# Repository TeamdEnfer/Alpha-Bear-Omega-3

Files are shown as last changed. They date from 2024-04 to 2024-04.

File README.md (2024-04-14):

# Alpha-Bear-Omega-3 ($\alpha-$:bear: $-\Omega-\pi$)

  

$\alpha-$:bear: $-\Omega-\pi$ | The **better-ish**(?) quadruped robot | UdeS-GRO-68

Inspired by project [QuadrUS](https://github.com/olivierfournier2/S4H2021-QuadrUS), Boston Dynamics' [Spot](https://bostondynamics.com/products/spot/) and MIT's [mini cheetah](https://news.mit.edu/2019/mit-mini-cheetah-first-four-legged-robot-to-backflip-0304),  $\alpha-$:bear: $-\Omega-\pi$ is a quadruped robot bear made by six robotics engineering students from [Université de Sherbrooke](https://www.usherbrooke.ca/).

## Original Contributors

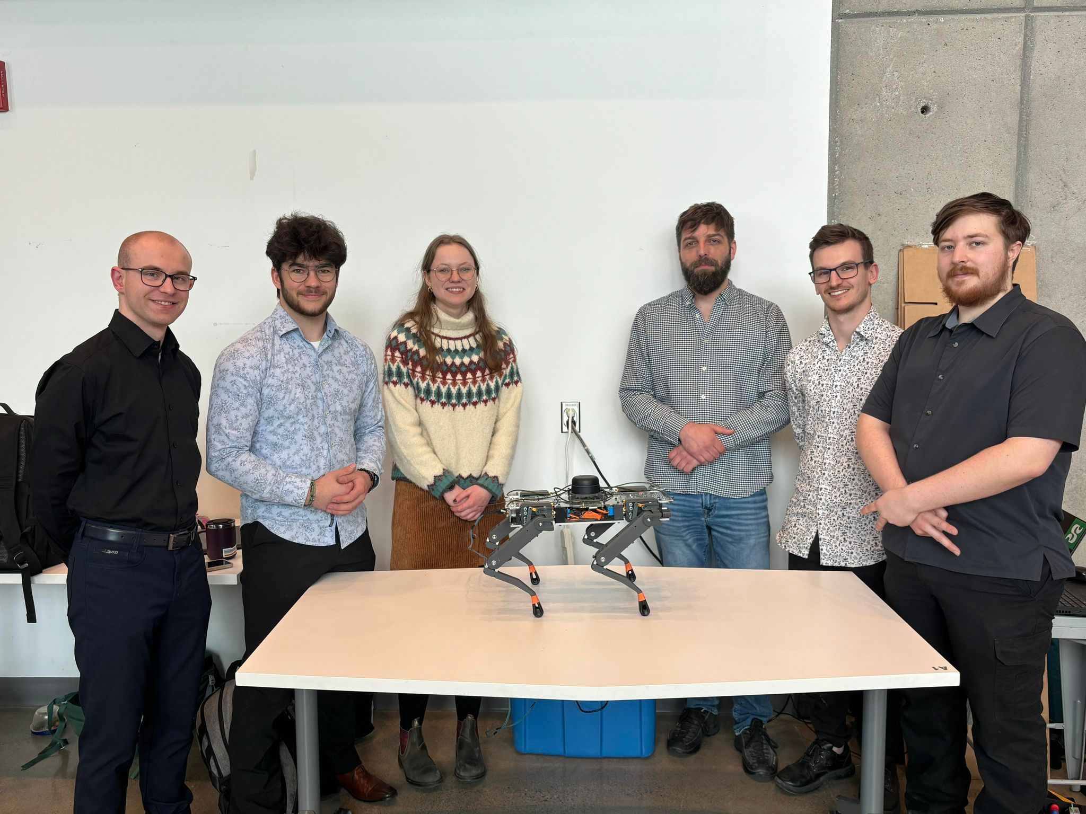
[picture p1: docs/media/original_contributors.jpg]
original_contributors


**From left to right:**

[Marc-Olivier Fecteau](https://github.com/MarcOlivierFecteau)  
[Hubert Houle](https://github.com/Hubert-Houle)  
[Justine Landry](https://github.com/justinelandry2)  
[Jonathan Perron](https://github.com/JPerron774)  
[Alex Jacques](https://github.com/AlexJacquesUS)  
[Thomas-Xavier Guimont](https://github.com/Revixa1)  

### A word from the authors

> We could say that when we chose to make a quadruped robot from scratch in 12 weeks, we wanted to prove to ourselves that we could achieve anything by working together, but we really just wanted to make something cool, and when brainstorming, the idea of a robot bear came up. Why a bear? Because bears can't be intimidated by dogs; thenceforth, robot bears are inherently better.

## Final product

gif_robot

## Table of contents

- [Development environment](#development-environment)
  - [Pre-requisites](#pre-requisites)
  - [Dependencies installation](#dependencies-installation)
  - [Using the installation script](#using-the-installation-script)
- [Robot environment](#robot-environment)
  - [System requirements](#system-requirements)
  - [Packages](#rpi-packages)
  - [Setup SSH](#setup-ssh)

## Development environment

### Pre-requisites

#### Operating system

- [Ubuntu 20.04 LTS](https://releases.ubuntu.com/focal/)

#### Packages

***N.B.*** The [installation script](#using-the-installation-script) installs most of the required packages. It is recommended to first run the script, and then [install the missing dependencies](#dependencies-installation).

- [ROS Noetic](http://wiki.ros.org/noetic/Installation/Ubuntu)
- Rviz: choose `Desktop-Full Install` option when installing ROS
- [CHAMP | champ](https://github.com/chvmp/champ)
- [CHAMP | champ setup assistant](https://github.com/chvmp/champ_setup_assistant)
- [Webots](https://cyberbotics.com/)
- [ROS Joy](http://wiki.ros.org/joystick_drivers)

### Dependencies installation

- Go to [ros-noetic installation page](https://wiki.ros.org/noetic/Installation/Ubuntu) and install ros-noetic.

- Install all dependencies for kinematics:

```bash
sudo apt install python3-pip ros-noetic-joy ros-noetic-rosserial ros-noetic-rosserial-python ros-noetic-rosserial-arduino
```

- Install all depencies for control:

```bash
sudo apt install ros-noetic-ros-control ros-noetic-robot-state-publisher ros-noetic-control-msgs
```

### Using the installation script

&emsp;***N.B.*** Cloning the repository and using the installation script, a **catkin workspace** is initialized, so there's no need to do this procedure.

Choose the directory you want the project cloned into (`~` by default):

```bash
cd ~/<path_to_directory>
```

Then, type:

```bash
git clone --recursive https://github.com/TeamdEnfer/Alpha-Bear-Omega-3.git
```

Then, go into the project repository, launch the install script, and choose what you want to install (`all` option is recommended for first install):

```bash
cd Alpha-Bear-Omega-3
source install.sh
```

Finally, go into the **catkin workspace** and build the ROS workspace:

```bash
cd control/ros_ws
catkin_make
```

The ROS environment should now be set up and ready to work with.

Project setup notes:

> - Every time a non-`.launch` file is modified, do `catkin_make` in the **ros_ws** directory to update the executables.
> - Every time a new terminal is opened, run the `source ./install.sh` script with option `6` to source the ROS setup files. Alternatively, add the command to the `.bashrc` file to automate the process.

## Robot environment

### System requirements

- RaspberryPi 4 (Tested with 8GB RAM)
- [Ubuntu 20.04 LTS](https://releases.ubuntu.com/focal/) (Tested with Server install)

&emsp;***Authors note:*** though we recommend installing Ubuntu Server on the RPi 4, our experience with tha installation was "painful and full of adventures". Good luck!

### RPi Packages

- [ROS Noetic](http://wiki.ros.org/noetic/Installation/Ubuntu)

### Setup SSH

- [Setup RPi as Wi-Fi access point](https://gist.github.com/ExtremeGTX/ea1d1c12dde8261b263ab2fead983dc8)

To access the RPi, type:

```bash
ssh <RPi_name>@<RPi_access_point>
```

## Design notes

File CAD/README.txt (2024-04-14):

Voici une description de la nomenclature pour les fichier de CAD pour le projet de session S4 en génie robotique
Les nom des fichiers sont en minuscule avec des _ pour séparer les mots.

x_y_concept_composante_extra_extra_z
_______________________________________________________________________________________
x:   		Choix de Conception Générale
		 	-0:Système avec poulie dentelée et courroie
_______________________________________________________________________________________
y:   		Version du concept Général
			-1: Système de poulie pour le Tibia et pour le Fémur
		 	-2: Système de poulie pour le Tibia et Barre pour le Fémur
_______________________________________________________________________________________
concept:	pour l'instant, représente le choix de conception comme x mais 
		sera décrit en mot. **sujet à changement vue la répétition
		 	-belt
			-directDrive 	
_______________________________________________________________________________________
composante:   	Nom de la pièce en question
			-body
		 	-femur
		 	-shaft
		 	-bar_trouee
_______________________________________________________________________________________
extra_extra:	Utilisée pour donner des informations suplémentaires sur la pièce.
		 	-60mm_en_L
		 	-simple_right
			-court
_______________________________________________________________________________________
z:   		Version de la pièce particulière auquel le nom est attaché.
_______________________________________________________________________________________

QUELQUES EXEMPLES:
	0_2_1_belt_epaule_1:	première version de l'épaule pour le système de drive belt pour
				le tibia et la barre pour le fémur
	0_0_2_belt_femur_une_piece1_0

*À noter qu'il est possible qu'une même pièce soit utilisé dans deux concept différent.
 Dans ce cas, le numéro de la version origionale est concervé.

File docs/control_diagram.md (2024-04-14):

# ROS | Nodes and topics diagram

::: mermaid

%%{ init: { 'flowchart': { 'curve': 'catmullRom' } } }%%

flowchart TB;
    subgraph RPi4B
        direction TB
        PiNode([RPi 4B])
        rplidar[[RPLIDAR]]

        rplidar -- distances --> PiNode
    end

    subgraph CHAMP
        direction LR
        velocity_smoother([velocity smoother])
        trajectory_controller([trajectory controller])
        teleop([teleop])

        imu/data[IMU data]
    end

    subgraph Arduino Mega
        direction BT
        ArduiNode([Arduino Mega])
        servos[["Servos (x12)"]]

        ArduiNode -- "servo cmd" --> servos
    end

    subgraph Arduino Uno
        direction TB
        BNode([Arduino Uno])
        bno[[BNO]]
        bno-- quaternion --> BNode
    end

    bno_feedback_topic[BNO feedback]

    BNode --> bno_feedback_topic
    bno_feedback_topic --> imu/data
    
    subgraph GUI
        GUI_Node([GUI])
    end

    servo_id_topic[servo id]
    servo_cmd_topic[servo cmd]

    GUI_Node --> servo_id_topic
    GUI_Node --> servo_cmd_topic

    subgraph Controller
        direction TB
        joystick[[Controller]]
        joyNode([Joy])

        joystick -- inputs --> joyNode
        joyNode -- magic --> teleop

    end
:::

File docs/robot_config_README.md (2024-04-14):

Fichiers à modifier pour champ

# Chemin des fichiers de configuration du robot

**URDF:** control/ros_ws/src/alphabearomega3/worlds/Robot  
**Joints:** control/ros_ws/src/alphabear_config/config/joints/joints.yaml  
**Links:** control/ros_ws/src/alphabear_config/config/links/links.yaml  
**Gait:** control/ros_ws/src/alphabear_config/config/gait/gait.yaml  
**Référence des paramètres du gait:** control/ros_ws/src/champ_setup_assistant/docs/images/gait_parameters.png  

# Paramètres du gait

### Paramètres à ne pas modifier

* knee_orientation
* pantograph_leg

### Paramètres pouvant être modifiés

* **odom_scaler :** facteur d'échelle pour compensation d'erreurs d'odométrie [1.0, 1.2]
* **max_linear_velocity_x :** vitesse max avant/arrière (m/s)
* **max_linear_velocity_y :** vitesse max déplacement vers gauche/droite (m/s)
* **max_angular_velocity_z :** vitesse max rotation (rad/s)
* **com_x_translation :** offset du point de référence dans l'axe X (i.e. compenser si centre de masse de la jambe pas aligné avec l'épaule) (m)
* **swing_height :** distance entre le sol et le centre de la patte au point le plus haut de l'élévation (m)
* **stance_depth :** delta distance du genou au point le plus bas durant un cycle (m)
* **stance_duration :** temps qu'une jambe passe appuyée au sol durant un cycle (s)
* **nominal_height :** distance entre l'épaule et le sol durant un cycle (m)

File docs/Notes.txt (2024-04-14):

En regardant Quadrus, l'interaction cmd<-->feedback ressemble a ceci:

Sur le arduino:

    Setup:
        initialisation (voir rosInit dans qd_hw_control.cpp)
            -Dans l'init, on le subscriber cmd_sub surveille le topic hw_cmd (voir definition de cmd_topic)
            -Dans l'init, on advertise le publisher feedback_pub, qui publish sur le topic hw_feedback (voir definition de feedback_topic)

    Subscriber:
        -Le subscriber prend des message multiarray
        -Surveille le topic cmd_topic
        -Utilise la fonction subscriberCallback
            -Cette fonction recois les angle (via hw_cmd) et envoie la commande aux moteurs
    
    Publisher:
        -Le publisher (feedback_pub) envoie des message multiarray et est lier au topic hw_feedback

    Loop:
        -Utilise la fonction readAngles, laquelle va chercher les angles et les store dans le message multiarray feedback_msg
        -Publish feedback_msg avec le publisher feedback_pub.
        -spinonce()
        -delay selon la frequence voulue

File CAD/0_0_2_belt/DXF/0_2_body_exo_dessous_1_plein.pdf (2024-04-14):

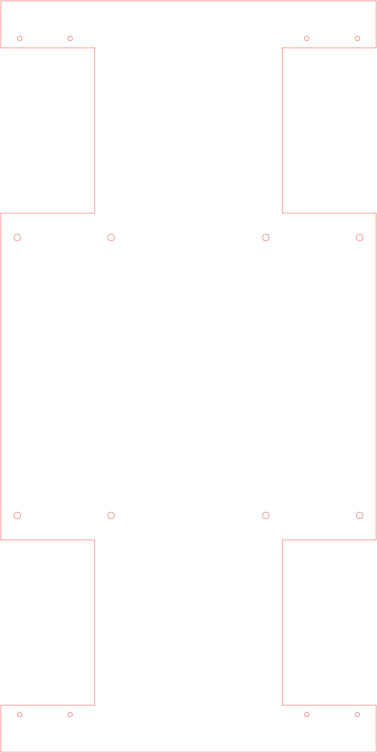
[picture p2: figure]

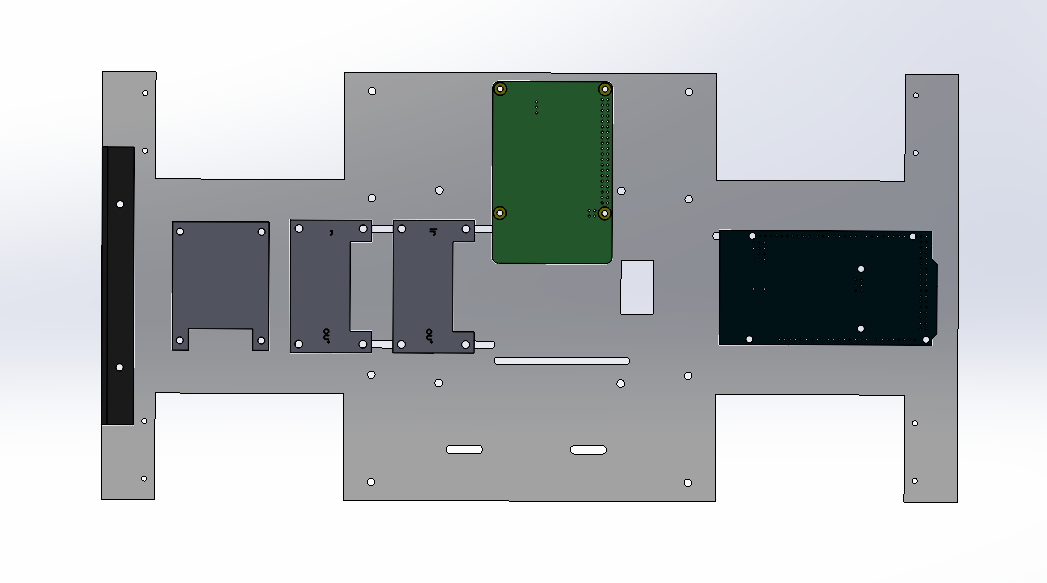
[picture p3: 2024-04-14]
docs/CAD_pictures/Electronics_layout.png

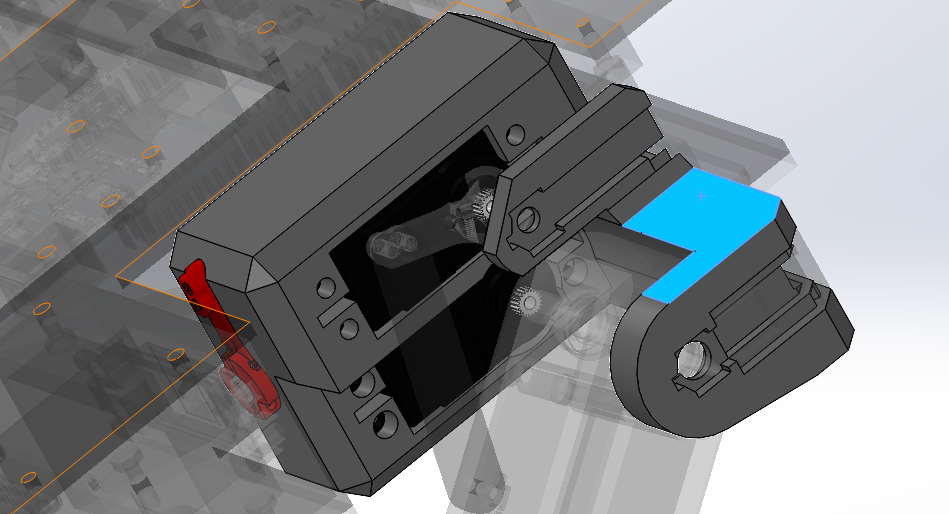
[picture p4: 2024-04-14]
docs/CAD_pictures/Shoulder_servo_ass.png

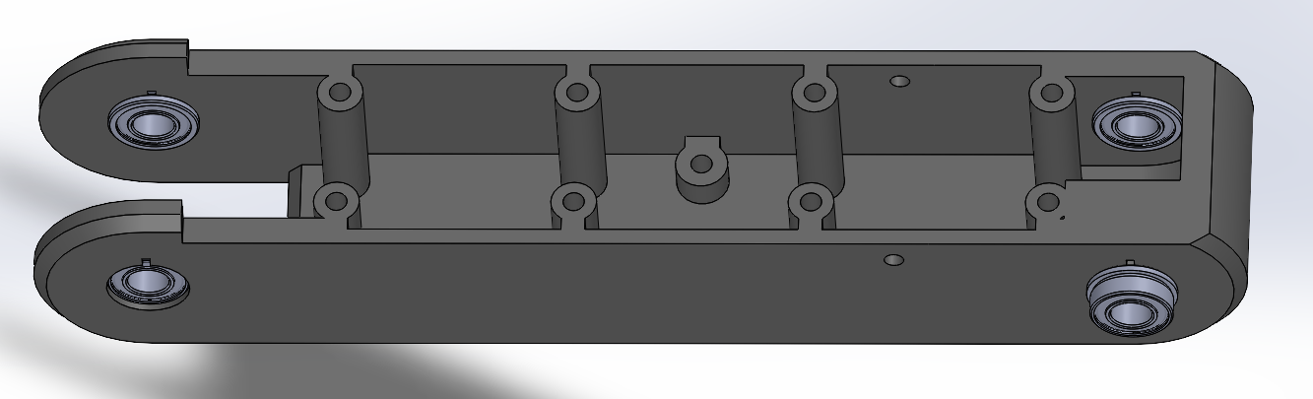
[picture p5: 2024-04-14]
docs/CAD_pictures/femur_bearings.png

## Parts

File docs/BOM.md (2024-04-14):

# BOM

## Hardware

- [ ] GT2 timing belt pulley 20 teeth 6.35mm bore (x4) [(Amazon)](https://a.co/d/ibclgCi)
- [ ] GT2 timing belt pulley 36 teeth 5mm bore (x4) [(Amazon)](https://a.co/d/5uwTJrM)
- [ ] 6.35mm flange coupling  connectors (x4) [(Amazon)](https://a.co/d/h0BUPP9)

## Electronics

- [ ] Arduino Mega 2560 Rev3 [(Arduino)](https://store-usa.arduino.cc/products/arduino-mega-2560-rev3?selectedStore=us)
- [ ] Arduino Uno Rev3 [(Arduino)](https://store-usa.arduino.cc/products/arduino-uno-rev3?selectedStore=us)
- [ ] Raspberry Pi 4 Model B [(Canakit)](https://www.canakit.com/raspberry-pi-4-8gb.html) | [(PiShop.ca)](https://www.pishop.ca/product/raspberry-pi-4-model-b-8gb/) (8GB RAM used)
- [ ] Adafruit BNO055 [(Adafruit)](https://www.adafruit.com/product/2472)
- [ ] Slamtec RPLIDAR A3 [(RobotShop)](https://ca.robotshop.com/fr/products/slamtec-rplidar-a3-360-laser-scanner-25-m)
- [ ] 35 kg.cm servomotors (x12) [(Amazon)](https://www.amazon.ca/s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)
- [ ] 12V-5V DC-DC USB-C converter [(Amazon)](https://a.co/d/4bkU4Bg)
- [ ] 20A 300W 6-40V to 1.2-36V adjustable DC-DC converter (x2) [(Amazon)](https://a.co/d/coVxflM)
- [ ] Power supply: 180W laptop charger (we used one that had a broken cable, so we soldered our own cable)
- [ ] 22|20 AWG wire (for data cables)
- [ ] (At least) 18 AWG wire (for power cables)
- [ ] Dupont connectors
- [ ] U-Type fork terminal electrical wire crimp connectors [(Amazon)](https://www.amazon.ca/s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)
- [ ] WAGO wire connectors [(Amazon)](https://www.amazon.ca/s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)

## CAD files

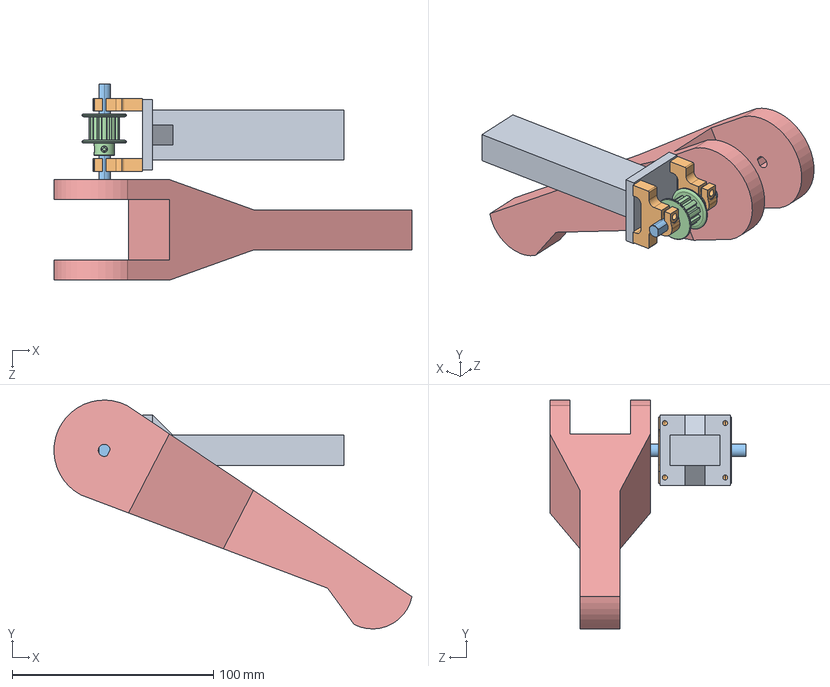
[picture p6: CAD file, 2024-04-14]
CAD/0_0_2_belt_BACK-UP_19_JANVIER/Assem1_tibia_2.SLDASM
177.9 x 113.7 x 97.6 mm
0_0_2_belt_tibia_1
634068.step
1277N711_Corrosion-Resistant Timing Belt Pulley
0_0_1_belt_tibia_1

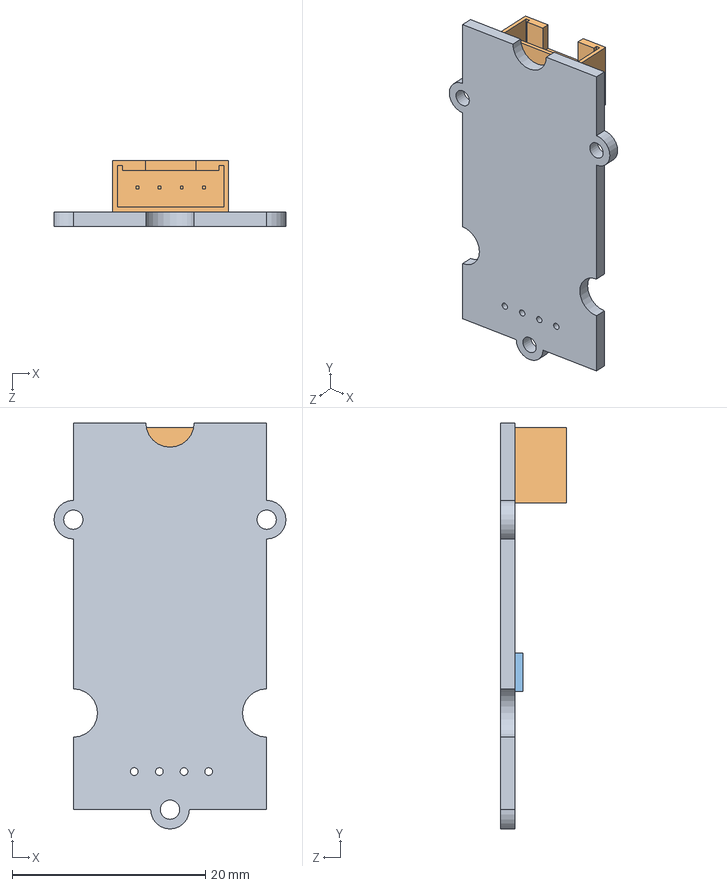
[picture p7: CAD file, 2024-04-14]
CAD/CAD_Web/Grove IMU.SLDASM
24.0 x 42.0 x 6.80 mm
Grove IMU Board
Grove Connecteur
MPU9150

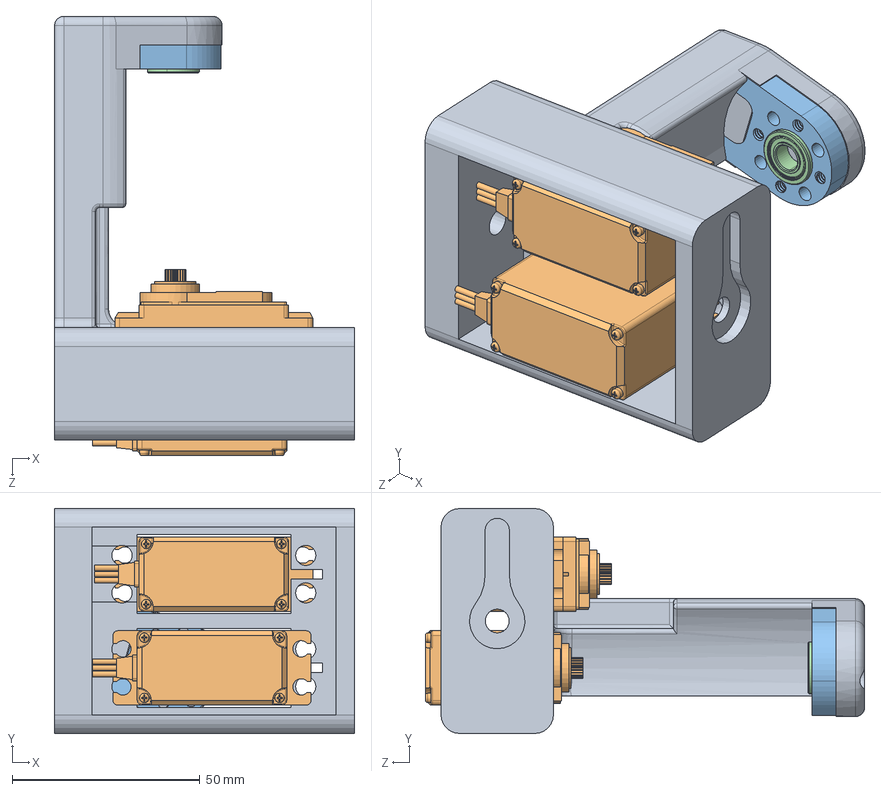
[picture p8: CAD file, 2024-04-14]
CAD/0_0_2_belt/0_2_epaule_1.SLDASM
80.0 x 60.0 x 117.2 mm
0_2_epaule_sprint2_deux_config_JO
hs-422_sws x 2
545404_shaft_adapter_90
535198_bearing

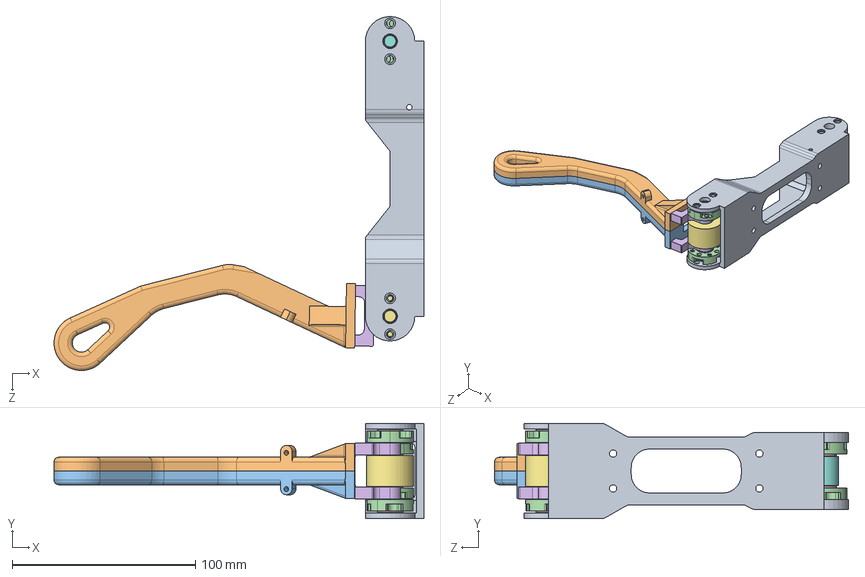
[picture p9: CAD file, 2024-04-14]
CAD/0_0_3_Final/Alexx/0_2_jambe_1.SLDASM
201.8 x 52.0 x 193.1 mm
0_2_femur_une_piece_1
0_2_tibia_2_D
0_2_tibia_2_G
545440.step x 4
535198_bearing x 4
0_2_poulie_grosse_home
0_2_poulie_petite_home

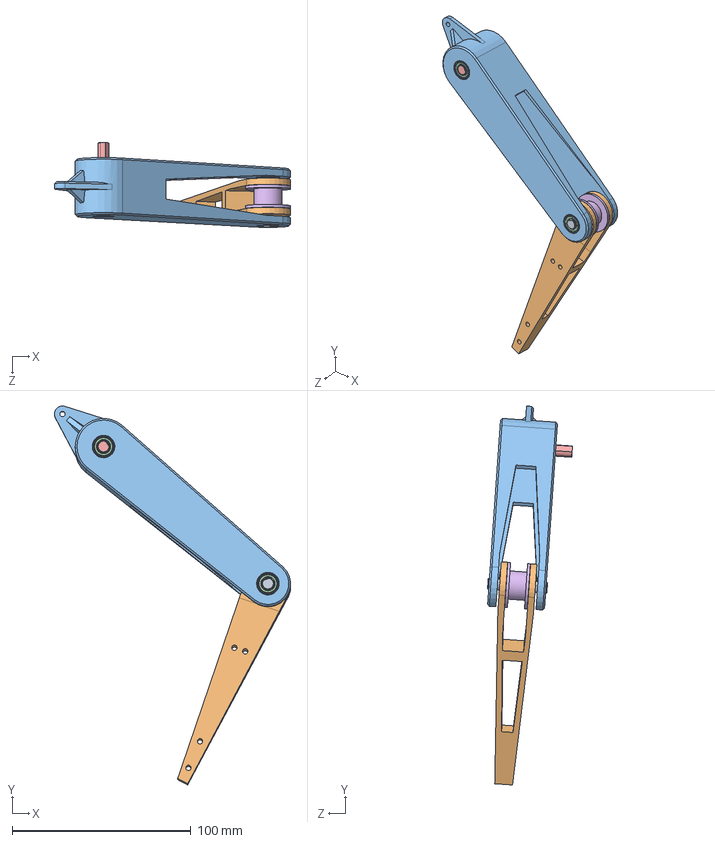
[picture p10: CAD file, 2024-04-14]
CAD/Marco/Marco_concept_SP01_v2/jambe_assemblage.SLDASM
132.3 x 212.3 x 47.6 mm
634088_12in_shaft_cut_tibia
tibia_v2
femur_v2
535198_bearing x 4
634088_12in_shaft_cut_femur
poulie_at_home

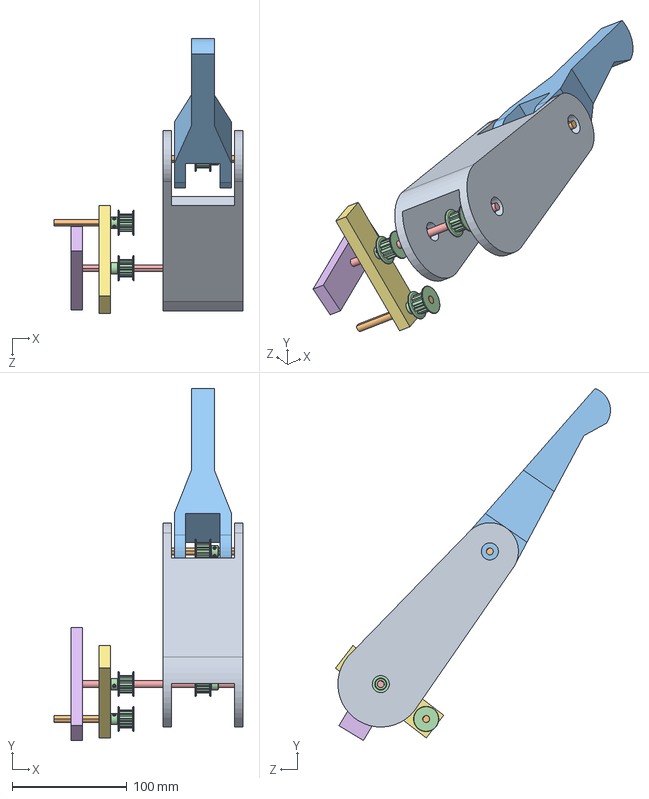
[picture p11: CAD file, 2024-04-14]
CAD/0_0_1_belt/Assem1.SLDASM
165.0 x 307.4 x 240.2 mm
0_0_1_belt_femur_1
0_0_1_belt_6mmShaft_1 x 2
0_0_1_belt_tibia_1
1277N711_Corrosion-Resistant Timing Belt Pulley x 4
0_0_1_belt_6mmX15mmShaft_1
0_0_1_belt_6mm_manivelle_1
0_0_1_belt_guideShaft75mm_1

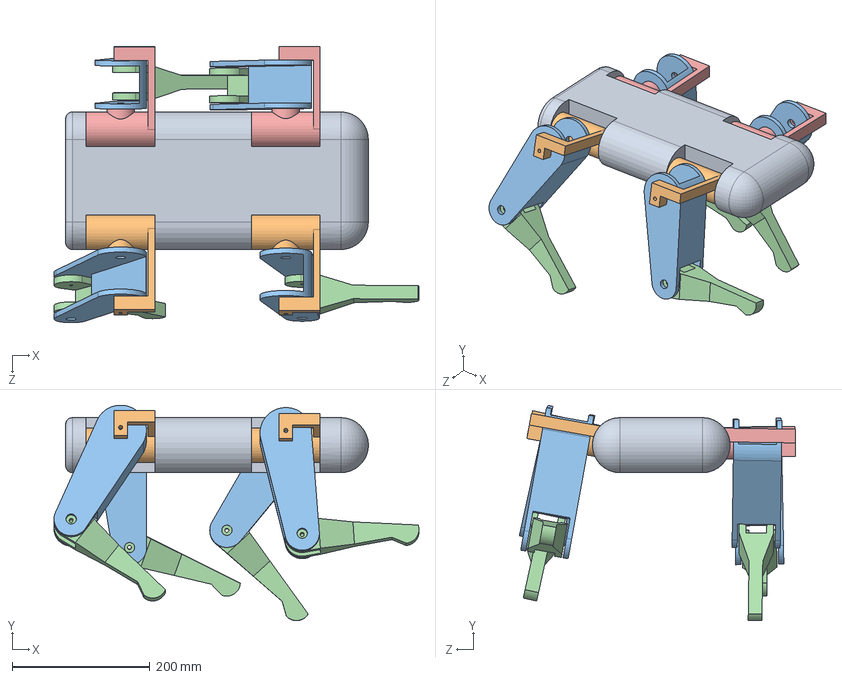
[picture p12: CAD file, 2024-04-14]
CAD/0_0_2_belt_BACK-UP_19_JANVIER/0_1_assemblage_robot_complet_1.SLDASM
530.3 x 313.1 x 401.6 mm
0_0_1_belt_body
0_0_1_belt_epaule_1 x 2
0_0_1_belt_femur_1 x 4
0_0_1_belt_tibia_1 x 4
0_0_1_belt_epaule_l_1 x 2

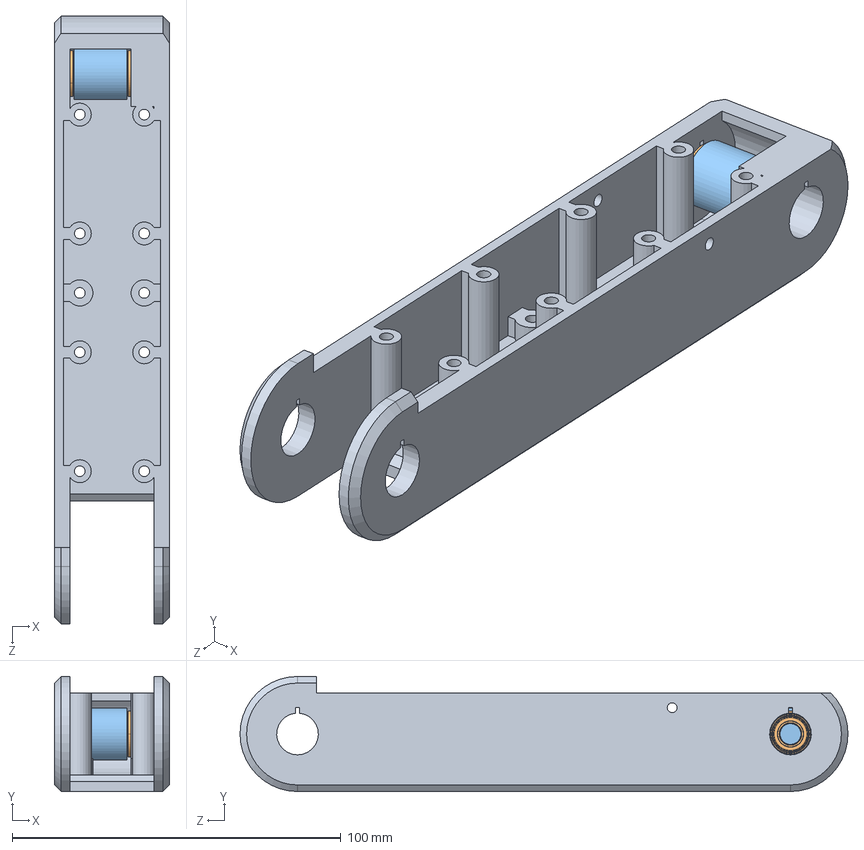
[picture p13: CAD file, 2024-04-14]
CAD/0_0_3_belt/Assem1.SLDASM
35.0 x 35.0 x 185.0 mm
0_0_3_femur_ferme_dessous_1
535198_bearing x 2
0_2_poulie_petite_home

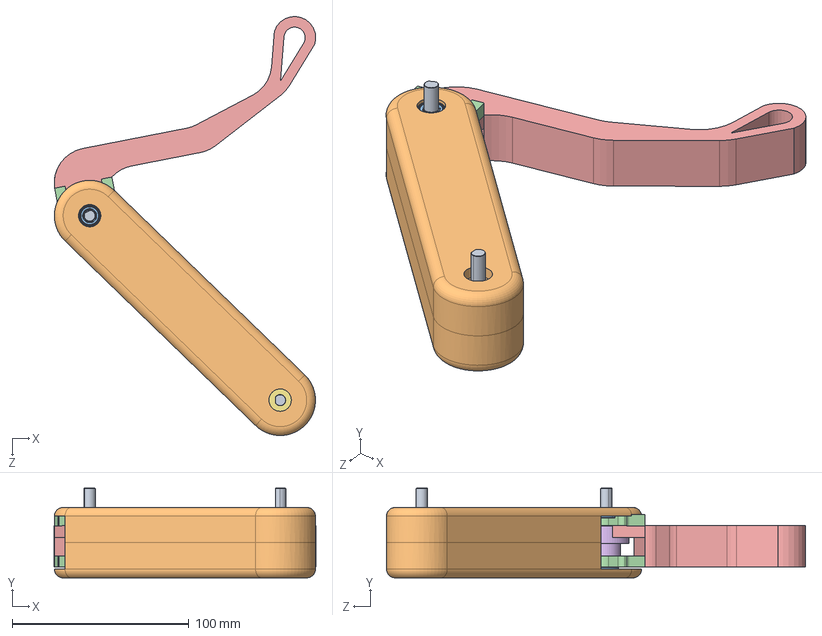
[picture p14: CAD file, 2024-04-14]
CAD/0_0_3_belt/0_0_3_belt_Assem1.SLDASM
147.9 x 50.8 x 237.0 mm
634068.step x 2
0_0_3_femur_simple_1 x 2
535198_bearing x 2
0_0_3_tibia_simple_1
0_2_poulie_grosse_home
0_2_poulie_petite_home

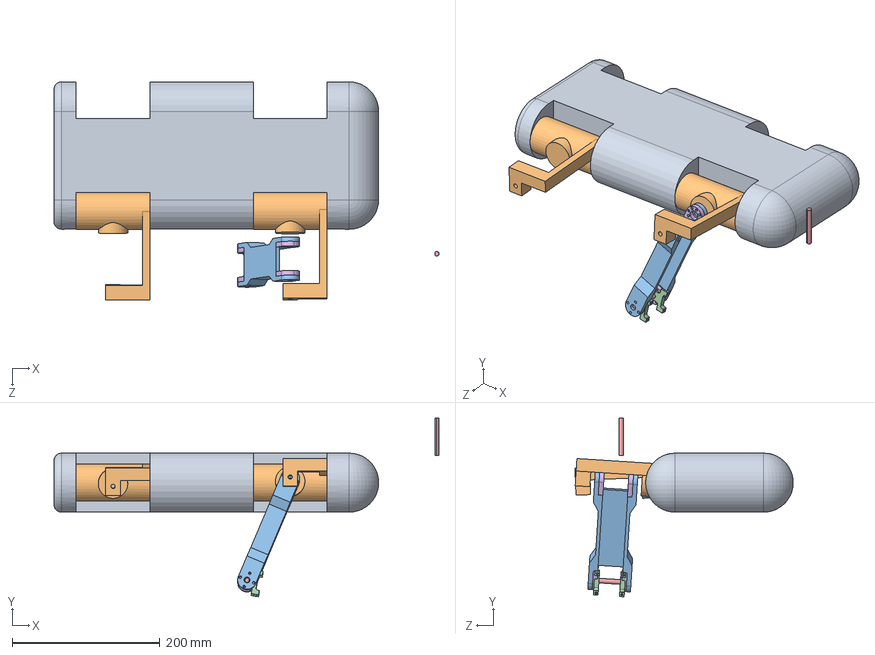
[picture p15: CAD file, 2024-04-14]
CAD/0_0_2_belt_BACK-UP_19_JANVIER/0_2_assemblage_robot_complet_1.SLDASM
521.7 x 242.2 x 295.9 mm
0_0_1_belt_body
0_0_1_belt_epaule_1 x 2
0_0_2_belt_femur_une_piece1_0
634068.step x 2
545404_shaft_adapter_90 x 4

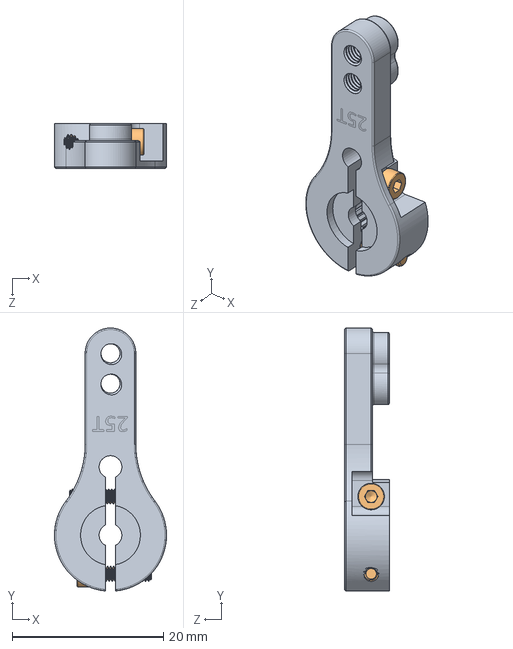
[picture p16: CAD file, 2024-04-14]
CAD/CAD_Web/SERVO ARM HORN 25T ALUMINIUM/SERVO ARM HORN WITH FASTENERS.SLDASM
14.8 x 34.7 x 5.90 mm
SERVO ARM HORN 25T ALUMINIUM
M2 CAP HEAD SOCKET SCREW x 2

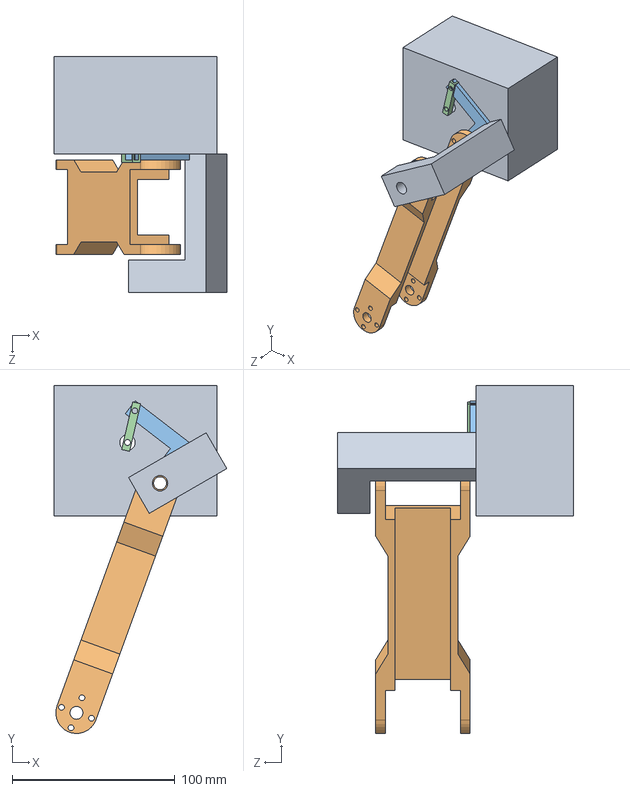
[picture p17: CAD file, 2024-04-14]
CAD/0_0_2_belt_BACK-UP_19_JANVIER/0_2_assemblage_sprint1_1.SLDASM
106.0 x 213.6 x 145.0 mm
0_0_2_belt_epaule_R_1
0_0_2_belt_femur_une_piece1_0
0_0_2_belt_90mm_bar_trouee_enL
0_0_2_belt_20mm_bar_I

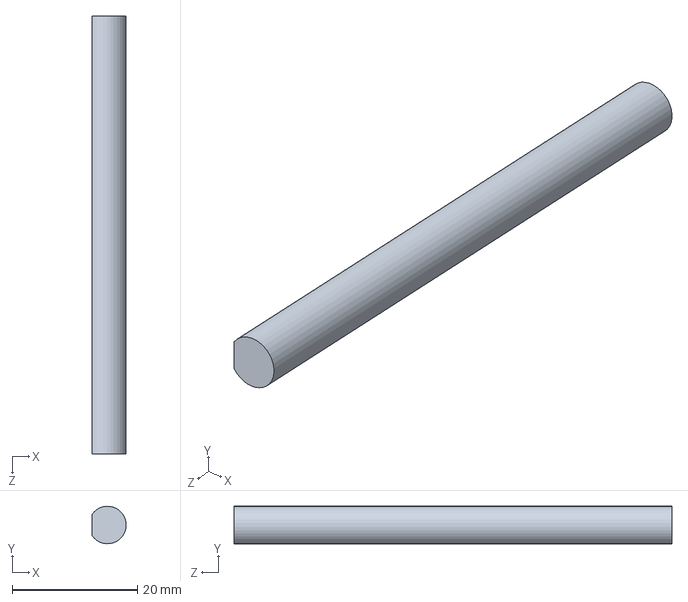
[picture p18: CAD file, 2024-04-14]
CAD/0_0_1_belt/0_0_1_belt_6mmShaft_1.SLDPRT
5.49 x 6.00 x 70.0 mm

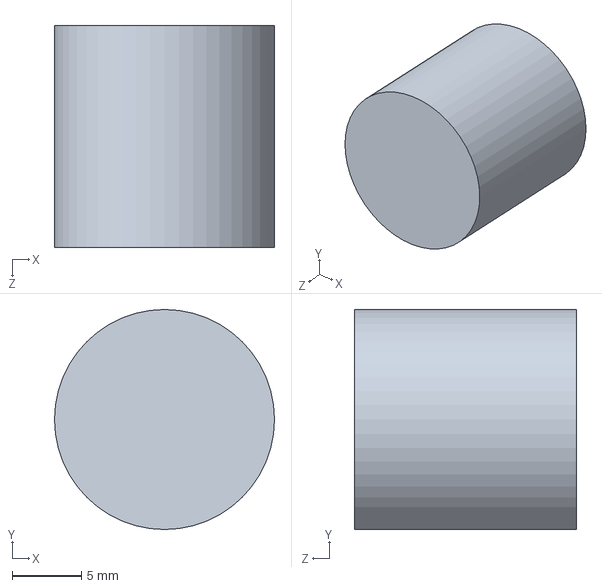
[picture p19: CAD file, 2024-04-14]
CAD/0_0_2_belt/0_2_poulie_petite_home.SLDPRT
15.9 x 15.9 x 16.0 mm

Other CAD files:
CAD/0_0_2_belt/0_2_jambe_1.SLDASM
CAD/0_0_2_belt/3MF/print_0_2_bar_trouee_en_C_35mm_1.3MF
CAD/0_0_2_belt/DXF/0_2_body_exo_dessous_1__EXO.DXF
CAD/0_0_1_belt/0_0_1_belt_6mmX15mmShaft_1.SLDPRT
CAD/0_0_1_belt/0_0_1_belt_6mm_manivelle_1.SLDPRT
CAD/0_0_1_belt/0_0_1_belt_femur_1.SLDPRT
CAD/0_0_1_belt/0_0_1_belt_guideShaft75mm_1.SLDPRT
CAD/0_0_1_belt/0_0_1_belt_tibia_1.SLDPRT
CAD/0_0_2_belt/0_2_bar_trouee_50mm_1.SLDPRT
CAD/0_0_2_belt/0_2_body_exo_dessous_1.SLDPRT
CAD/0_0_2_belt/0_2_body_exo_dessous_1_MEP.SLDDRW
CAD/0_0_2_belt/0_2_epaule_sprint2_deux_config.SLDPRT
CAD/0_0_2_belt/0_2_epaule_sprint2_deux_config_JO.SLDPRT
CAD/0_0_2_belt/0_2_femur_une_piece_1.SLDPRT
CAD/0_0_2_belt/0_2_poulie_grosse_home.SLDPRT
CAD/0_0_2_belt/0_2_spacer_avec_trou_1.SLDPRT
CAD/0_0_2_belt/0_2_support_abduction_servo_1.SLDPRT
CAD/0_0_2_belt/0_2_tibia_2_D.SLDPRT
CAD/0_0_2_belt/0_2_tibia_2_G.SLDPRT
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

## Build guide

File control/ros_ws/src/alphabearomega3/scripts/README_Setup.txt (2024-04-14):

Etapes pour starter ROS sur le Pi, ainsi que la communication Rosserial

1: SSH sur le pi
2: roscore &
3: rosrun rosserial_python serial_node.py /dev/ttyACM0 & 

Nom du topic: /servo
    Format du message: rostopic pub /servo  std_msgs/UInt16 "data: 0"
    ou data: est un angle donner a un servo lier a la pin D13

Nom du node: /serial_node

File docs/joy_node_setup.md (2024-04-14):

# Button mapping for controllers

Button maps for other controllers can be found [here](http://wiki.ros.org/joy#Application)

## Xbox One controller

### Axes

0: Joystick gauche: gauche <-> droite \[-32767, 32767\]  
1: gauche: haut <-> bas \[-32767, 32767\]  
2: Trigger (analog) gauche \[-32767, 32767\]  
3: Joystick droite: gauche <-> droite \[-32767, 32767\]  
4: Joystick droit: haut <-> bas \[-32767, 32767\]  
5: Trigger (analog) droite \[-32767, 32767\]  
6: D-pad gauche <-> droite {-32767, 32767}  
7: D-pad haut <-> bas {-32767, 32767}

	N.B. ROS: [-1.0, 1.0], {-1.0, 1.0}

### Boutons

0: A  
1: B  
2: X  
3: Y  
4: Bumper gauche  
5: Bumper droit  
6: Select  
7: Start  
8: Power/Menu  
9: Joystick gauche: appui  
10: Joystick droit: appui

## PlayStation 3 controller

### Axes
0: Joystick gauche: gauche <-> droite \[-32767, 32767\]  
1: gauche: haut <-> bas \[-32767, 32767\]  
2: Trigger (analog) gauche \[-32767, 32767\]  
3: Joystick droite: gauche <-> droite \[-32767, 32767\]  
4: Joystick droit: haut <-> bas \[-32767, 32767\]  
5: Trigger (analog) droite \[-32767, 32767\]

### Boutons

0: X  
1: O  
2: 🔺  
3: 🟥  
4: Bumper gauche  
5: Bumper droit  
6: Trigger gauche (bool)  
7: Trigger droit (bool)  
8: Select  
9: Start  
10: Power/Menu  
11: Trigger gauche: appui  
12: Trigger droit: appui  
13: D-pad Up  
14: D-pad Down  
15: D-pad Left  
16: D-pad Right

# Making the controller accessible by ROS joy node

```console
$ ls -l /dev/input/jsX
```

Output:  
	crw-rw-r--+ 1 root input 13, 0 Mar 12 08:05 /dev/input/jsX

if XX is rw: the device is configured properly.  
if XX is -- or r-, you need to:

```console
$ sudo chmod a+rw /dev/input/jsX
```

# Running the node

## prerequisites

### roscore

If the core hasn't been started yet, type:

```console
$ roscore
```

## Parameters

Below are examples of parameters that can be changed before running the node. For a complete list of parameters, see [the source documentation](http://wiki.ros.org/joy#Parameters).

```console
$ rosparam set joy_node/dev "/dev/input/jsX"
$ rosparam set joy_node/deadzone 0.25
```

    N.B. the deadzone parameter defaults to 0.05, but I find it too sensitive at that value. Value range: [0, 1]

## Starting the node

In a new terminal, type:

```console
$ roslaunch champ_teleop teleop.launch joy:=true
```

The champ_teleop node launches the joy node when the argument *joy* is set to true, so there is no need for *rosrun*.

To observe the commands read from the controller, in a new terminal, type:

```console
$ rostopic echo joy
```

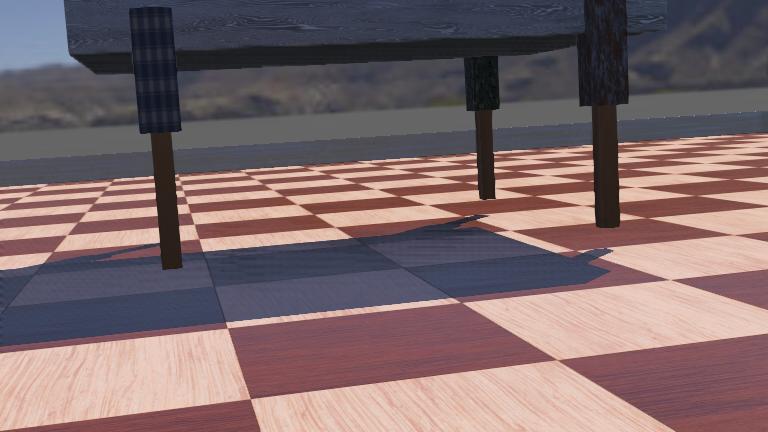
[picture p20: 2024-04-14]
control/ros_ws/install/share/alphabearomega3/worlds/.bear_topia.jpg

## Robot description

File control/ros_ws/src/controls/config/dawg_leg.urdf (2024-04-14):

<robot name="test_robot">
   <link name="link1" />
   <link name="link2" />
   <link name="link3" />
 
   <joint name="Femur_FR" type="continuous">
     <parent link="link1"/>
     <child link="link2"/>
   </joint>
 
   <joint name="Tibia_FR" type="continuous">
     <parent link="link1"/>
     <child link="link3"/>
   </joint>
 </robot>

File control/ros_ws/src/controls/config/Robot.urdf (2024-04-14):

<?xml version="1.0"?>
<robot xmlns:xacro="http://ros.org/wiki/xacro" name="robot">

    <xacro:include filename="materials.xacro" />
    <xacro:include filename="constants.xacro" />
    <xacro:include filename="include.xacro" />

    <link name="world"></link>

    <joint name="body_joint" type="fixed">
        <origin xyz="0 0 0" rpy="0 0 0"/>
        <parent link="world"/>
        <child link="body_link"/>
    </joint>

    <link name="body_link">
        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
    </link>

    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
    <xacro:servo_joint id="FLS" origin="-0.25 0.3 0" parent="body_link" child="FLS_link" axis="shoulder_axis" lower_limit=${-pi/4} upper_limit=${pi/4}/>
    <xacro:generic_link id="FLS" origin="-0.25 0.3 0" size="shoulder_sketch_size" material="white"/>

    <xacro:servo_joint id="FLF" origin="-0.05 0 0" parent="FLS_link" child="FLT_link" axis="leg_axis" lower_limit="0" upper_limit=${pi/2}/>
    <xacro:generic_link id="FLF" origin="-0.05 0 0" size="femur_sketch_size" material="white"/>

    <xacro:servo_joint id="FLT" origin="0 0 -0.15" parent="FLF_link" child="FLB_link" axis="leg_axis" lower_limit="0" upper_limit=${pi/2}/>
    <xacro:generic_link id="FLT" origin="0 0 -0.15" size="tibia_sketch_size" material="white"/>

    <joint name="FLB_joint" type="fixed">
        <origin xyz="0 0 -0.085" rpy="0 0 0"/>
        <parent link="FLT_link"/>
        <child link="FLB_link"/>
    </joint>

    <link name="FLB_link">
        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
    </link>

    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
    <xacro:servo_joint id="FRS" origin="0.25 0.3 0" parent="body_link" child="FRS_link" axis="shoulder_axis" lower_limit=${-pi/4} upper_limit=${pi/4}/>
    <xacro:generic_link id="FRS" origin="0.25 0.3 0" size="shoulder_sketch_size" material="white"/>

    <xacro:servo_joint id="FRF" origin="0.05 0 0" parent="FRS_link" child="FRT_link" axis="leg_axis" lower_limit="0" upper_limit=${pi/2}/>
    <xacro:generic_link id="FRF" origin="0.05 0 0" size="femur_sketch_size" material="white"/>

    <xacro:servo_joint id="FRT" origin="0 0 -0.15" parent="FRF_link" child="FRB_link" axis="leg_axis" lower_limit="0" upper_limit=${pi/2}/>
    <xacro:generic_link id="FRT" origin="0 0 -0.15" size="tibia_sketch_size" material="white"/>

    <joint name="FRB_joint" type="fixed">
        <origin xyz="0 0 -0.085" rpy="0 0 0"/>
        <parent link="FRT_link"/>
        <child link="FRB_link"/>
    </joint>

    <link name="FRB_link">
        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
    </link>


    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
    <xacro:servo_joint id="RLS" origin="-0.25 -0.3 0" parent="body_link" child="RLS_link" axis="shoulder_axis" lower_limit=${-pi/4} upper_limit=${pi/4}/>
    <xacro:generic_link id="RLS" origin="-0.25 -0.3 0" size="shoulder_sketch_size" material="white"/>

    <xacro:servo_joint id="RLF" origin="-0.05 0 0" parent="RLS_link" child="RLT_link" axis="leg_axis" lower_limit="0" upper_limit=${pi/2}/>
    <xacro:generic_link id="RLF" origin="-0.05 0 0" size="femur_sketch_size" material="white"/>

    <xacro:servo_joint id="RLT" origin="0 0 -0.15" parent="RLF_link" child="RLB_link" axis="leg_axis" lower_limit="0" upper_limit=${pi/2}/>
    <xacro:generic_link id="RLT" origin="0 0 -0.15" size="tibia_sketch_size" material="white"/>

    <joint name="RLB_joint" type="fixed">
        <origin xyz="0 0 -0.085" rpy="0 0 0"/>
        <parent link="FRT_link"/>
        <child link="FRB_link"/>
    </joint>

    <link name="RLB_link">
        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
    </link>

    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
    <xacro:servo_joint id="RRS" origin="0.25 -0.3 0" parent="body_link" child="RRS_link" axis="shoulder_axis" lower_limit=${-pi/4} upper_limit=${pi/4}/>
    <xacro:generic_link id="RRS" origin="0.25 -0.3 0" size="shoulder_sketch_size" material="white"/>

    <xacro:servo_joint id="RRF" origin="0.05 0 0" parent="RRS_link" child="RRT_link" axis="leg_axis" lower_limit="0" upper_limit=${pi/2}/>
    <xacro:generic_link id="RRF" origin="0.05 0 0" size="femur_sketch_size" material="white"/>

    <xacro:servo_joint id="RRT" origin="0 0 -0.15" parent="RRF_link" child="RRB_link" axis="leg_axis" lower_limit="0" upper_limit=${pi/2}/>
    <xacro:generic_link id="RRT" origin="0 0 -0.15" size="tibia_sketch_size" material="white"/>

    <joint name="RRB_joint" type="fixed">
        <origin xyz="0 0 -0.085" rpy="0 0 0"/>
        <parent link="RRT_link"/>
        <child link="RRB_link"/>
    </joint>

    <link name="RRB_link">
        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
    </link>

</robot>



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

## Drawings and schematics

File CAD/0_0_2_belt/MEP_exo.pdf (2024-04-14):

B

2

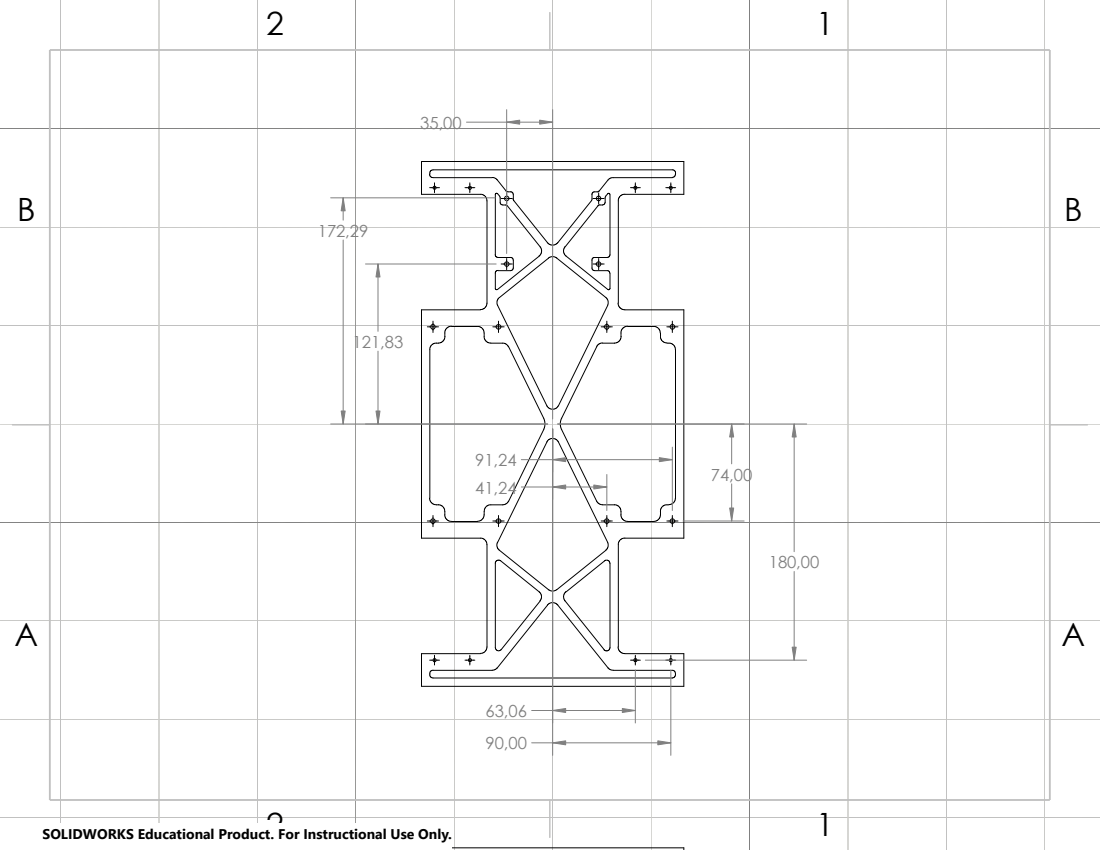
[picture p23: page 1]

SOLIDWORKS Educational Product. For Instructional Use Only.

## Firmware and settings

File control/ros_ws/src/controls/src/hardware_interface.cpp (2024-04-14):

#include <controls/hardware_interface.h>

#define PI 3.141592653
#define RAD2DEG 180/PI
#define DEG2RAD PI/180

bool ctrl_selector = false;
int leg_id = 0;         // [0, 11]; see 'config.h' for map
float leg_cmd = 0.0;    // cmd received from Arduino (deg)


Bear::Bear(ros::NodeHandle& nh) : nh_(nh) {
// Declare all JointHandles, JointInterfaces and JointLimitInterfaces of the robot.
    init();
    
// Create the controller manager
    controller_manager_.reset(new controller_manager::ControllerManager(this, nh_));
    
//Set the frequency of the control loop.
    loop_hz_= 100;
    // Sets the loop's period (ms)
    ros::Duration update_freq = ros::Duration(1.0/loop_hz_);
    
//Run the control loop
    my_control_loop_ = nh_.createTimer(update_freq, &Bear::update, this);

// Initializes publishers that communicate servo commands
// (FR) On publish les commande qui vont au servos
    commandPublisher = nh_.advertise<controls::Servo_cmd>("Command", 12);
    IMU_feedback_publisher = nh_.advertise<sensor_msgs::Imu>("imu/data" , 12);
    JointStatePublisher = nh_.advertise<sensor_msgs::JointState>("joint_states",12);

// Subscribes to ArduiNode
// (FR) On subscribe au ArduiNode
    Pot_callback = nh_.subscribe("pot_feedback_topic" , 12 , &Bear::Angles_callback , this);
    BNO_callback = nh_.subscribe("Feedback" , 12 , &Bear::IMU_callback, this);

// Subscribes to CHAMP controller
// (FR) on subscribe au controller champ
    champ_cmd = nh_.subscribe("/joint_group_position_controller/command" , 10 , &Bear::write , this);

// Subscribes to GUI topics for manual control of the legs
// (FR) on subscribe au topics du GUI pour pouvoir controller manuellement, et changer de controlleur
    GUI_cmd = nh_.subscribe("/servo_cmd_topic" , 12 , &Bear::GUI_CMD , this);
    GUI_id = nh_.subscribe("/servo_id_topic" , 12 , &Bear::GUI_ID , this);
    controller_selector = nh_.subscribe("/control_switch_flag" , 1 , &Bear::Selector , this);
}


// Class destructor
Bear::~Bear() {
}


// Class instance initialization method
void Bear::init() {
        
// TODO (2024-04-03): clean up commented codes
    //IMU_data.linear_acceleration.x = 0;
    //IMU_data.linear_acceleration.y = 0;
    //IMU_data.linear_acceleration.z = 0;

    // HWI for front left leg
    // (FR) HWI pour la jambe avant gauche
    jsHandle[0] = hardware_interface::JointStateHandle(("FL_shoulder_servo"), &pos[0], &vel[0], &eff[0]);
    joint_state_interface_.registerHandle(jsHandle[0]);

    jpHandle[0] = hardware_interface::JointHandle(joint_state_interface_.getHandle(("FL_shoulder_servo")), &cmd[0]);
    position_joint_interface_.registerHandle(jpHandle[0]);

    jsHandle[1] = hardware_interface::JointStateHandle(("FL_femur_servo"), &pos[1], &vel[1], &eff[1]);
    joint_state_interface_.registerHandle(jsHandle[1]);

    jpHandle[1] = hardware_interface::JointHandle(joint_state_interface_.getHandle(("FL_femur_servo")), &cmd[1]);
    position_joint_interface_.registerHandle(jpHandle[1]);

    jsHandle[2] = hardware_interface::JointStateHandle(("FL_tibia_servo"), &pos[2], &vel[2], &eff[2]);
    joint_state_interface_.registerHandle(jsHandle[2]);

    jpHandle[2] = hardware_interface::JointHandle(joint_state_interface_.getHandle(("FL_tibia_servo")), &cmd[2]);
    position_joint_interface_.registerHandle(jpHandle[2]);

    // HWI for front right leg
    // (FR) HWI pour la jambe avant droite
    jsHandle[3] = hardware_interface::JointStateHandle(("FR_shoulder_servo"), &pos[3], &vel[3], &eff[3]);
    joint_state_interface_.registerHandle(jsHandle[3]);

    jpHandle[3] = hardware_interface::JointHandle(joint_state_interface_.getHandle(("FR_shoulder_servo")), &cmd[3]);
    position_joint_interface_.registerHandle(jpHandle[3]);

    jsHandle[4] = hardware_interface::JointStateHandle(("FR_femur_servo"), &pos[4], &vel[4], &eff[4]);
    joint_state_interface_.registerHandle(jsHandle[4]);

    jpHandle[4] = hardware_interface::JointHandle(joint_state_interface_.getHandle(("FR_femur_servo")), &cmd[4]);
    position_joint_interface_.registerHandle(jpHandle[4]);

    jsHandle[5] = hardware_interface::JointStateHandle(("FR_tibia_servo"), &pos[5], &vel[5], &eff[5]);
    joint_state_interface_.registerHandle(jsHandle[5]);

    jpHandle[5] = hardware_interface::JointHandle(joint_state_interface_.getHandle(("FR_tibia_servo")), &cmd[5]);
    position_joint_interface_.registerHandle(jpHandle[5]);

    // HWI for rear left leg
    // (FR) HWI pour la jambe arriere gauche
    jsHandle[6] = hardware_interface::JointStateHandle(("RL_shoulder_servo"), &pos[6], &vel[6], &eff[6]);
    joint_state_interface_.registerHandle(jsHandle[6]);

    jpHandle[6] = hardware_interface::JointHandle(joint_state_interface_.getHandle(("RL_shoulder_servo")), &cmd[6]);
    position_joint_interface_.registerHandle(jpHandle[6]);

    jsHandle[7] = hardware_interface::JointStateHandle(("RL_femur_servo"), &pos[7], &vel[7], &eff[7]);
    joint_state_interface_.registerHandle(jsHandle[7]);

    jpHandle[7] = hardware_interface::JointHandle(joint_state_interface_.getHandle(("RL_femur_servo")), &cmd[7]);
    position_joint_interface_.registerHandle(jpHandle[7]);

    jsHandle[8] = hardware_interface::JointStateHandle(("RL_tibia_servo"), &pos[8], &vel[8], &eff[8]);
    joint_state_interface_.registerHandle(jsHandle[8]);

    jpHandle[8] = hardware_interface::JointHandle(joint_state_interface_.getHandle(("RL_tibia_servo")), &cmd[8]);
    position_joint_interface_.registerHandle(jpHandle[8]);

    // HWI for rear right leg
    // (FR) HWI pour la jambe arriere droite
    jsHandle[9] = hardware_interface::JointStateHandle(("RR_shoulder_servo"), &pos[9], &vel[9], &eff[9]);
    joint_state_interface_.registerHandle(jsHandle[9]);

    jpHandle[9] = hardware_interface::JointHandle(joint_state_interface_.getHandle(("RR_shoulder_servo")), &cmd[9]);
    position_joint_interface_.registerHandle(jpHandle[9]);

    jsHandle[10] = hardware_interface::JointStateHandle(("RR_femur_servo"), &pos[10], &vel[10], &eff[10]);
    joint_state_interface_.registerHandle(jsHandle[10]);

    jpHandle[10] = hardware_interface::JointHandle(joint_state_interface_.getHandle(("RR_femur_servo")), &cmd[10]);
    position_joint_interface_.registerHandle(jpHandle[10]);

    jsHandle[11] = hardware_interface::JointStateHandle(("RR_tibia_servo"), &pos[11], &vel[11], &eff[11]);
    joint_state_interface_.registerHandle(jsHandle[11]);

    jpHandle[11] = hardware_interface::JointHandle(joint_state_interface_.getHandle(("RR_tibia_servo")), &cmd[11]);
    position_joint_interface_.registerHandle(jpHandle[11]);

// Register all joints interfaces    
    registerInterface(&joint_state_interface_);
    registerInterface(&position_joint_interface_);
    // registerInterface(&positionJointSaturationInterface);    // 2024-04-03: Is this still usefull?

    //ros::Subscriber sub = nh_.subscribe("Feedback", 10 ,&Bear::fetchFeedback, this);// <std_msgs::Float64MultiArray> // 2024-04-03: Is this still usefull?
}



// This is the control loop
void Bear::update(const ros::TimerEvent& e) {
    elapsed_time_ = ros::Duration(e.current_real - e.last_real);
    //read();
    controller_manager_->update(ros::Time::now(), elapsed_time_);
    //write(elapsed_time_);
}

// Controller selector update method
void Bear::Selector(const std_msgs::Bool& controller_selector) {
    ctrl_selector = controller_selector.data;
}

// Servo ID update method (incorrectly named 'leg_id')
void Bear::GUI_ID(const std_msgs::Int8& GUI_id) {
    leg_id = GUI_id.data;
}

// Update servo cmd received from GUI
void Bear::GUI_CMD(const std_msgs::Float32& GUI_cmd) {
    leg_cmd = GUI_cmd.data;
}

//void Bear::read(const std_msgs::Float64MultiArray& Arduino_joint_position_topic){ // 2024-04-03: Is this still usefull?

// Read cmd msgs from Arduino
void Bear::Angles_callback(const controls::Servo_cmd Pot_callback) {
    for (int i = 0; i < NB_OF_JOINTS; i++) {
        pos[i] = Pot_callback.data[i] * DEG2RAD;
    }
}

// BNO data update method (incorrectly called IMU_callback)
void Bear::IMU_callback(const controls::BNO& BNO_callback) {
    // Linear acceleration
    IMU_data.linear_acceleration.x = BNO_callback.data[0];
    IMU_data.linear_acceleration.y = BNO_callback.data[1];
    IMU_data.linear_acceleration.z = BNO_callback.data[2];

    // Body orientation data (quaternions)
    IMU_data.orientation.x = BNO_callback.data[3]*DEG2RAD;
    IMU_data.orientation.y = BNO_callback.data[4]*DEG2RAD;
    IMU_data.orientation.z = BNO_callback.data[5]*DEG2RAD;
    IMU_data.orientation.w = BNO_callback.data[6]*DEG2RAD;

    for(int i = 0 ; i < 9 ; i++) {  // 8 potentiometers are used, so hard-coded 9
        IMU_data.linear_acceleration_covariance[i] = 0.0;
        IMU_data.orientation_covariance[i] = 0.0;
    }

	IMU_data.linear_acceleration_covariance[0]=0.0005;
	IMU_data.linear_acceleration_covariance[4]=0.0005;
	IMU_data.linear_acceleration_covariance[8]=0.0005;

    IMU_data.orientation_covariance[0] = 0.025;
	IMU_data.orientation_covariance[4] = 0.025;
	IMU_data.orientation_covariance[8] = 0.025
	;
    // Linear velocity
    IMU_data.angular_velocity_covariance[0] = -1;

    // Publish data to CHAMP controller
    IMU_feedback_publisher.publish(IMU_data);
}

// 2024-04-03: is still useful?
void Bear::fetchFeedback(const std_msgs::Float64MultiArray& feedback_message)
{
    //On s'attend a recevoir des lectures de IMU de la part du arduino via rosserial
    //On prend les lecture et on les met dans le JointStateHandle (jsHandle[i]) du joint approrier.

    
    for(int i = 0 ; i < NB_OF_JOINTS ; i++)
    {
        pos[i] = feedback_message.data[i];
    }
}

// Send cmds to servos received from controller
void Bear::write(trajectory_msgs::JointTrajectory champ_cmd) {

    // 2024-04-03: is this still useful?
    //On prend les messages de commande du controller, et on les mets dans un float64multiplearray, puis on les publish
	float ratio_pulleys_tibia=20.0f/36.0f;
    float OFFSET_03 = 2*PI/4;
    float OFFSET_69 = -2*PI/4;

    // Sending cmds with CHAMP controller
    if(ctrl_selector == false) {    // Could be changed to '!ctrl_selector'

/* Servo structure:
    1) Block = leg: [front left, front right, rear left, rear right]
    2) In the same block:
        i) Shoulder
        ii) Femur
        iii) Tibia
*/
        /* N.B. This section is FULL of magic numbers; to facilitate implementation the
         	equations of angle traduction (Champ command of leg position in radians to 			
         	arduino command of the servo position in degres) are implemented as offset for shoulders,
         	as quadratic fitting equation for the femurs and as ratios for the tibias.
         	
         	The femurs equations are fitted in excel. The data to fit comes from a simulation of a 4 bar linkage 
         	with the legs dimmensions in desmos (the link: https://www.desmos.com/calculator/vvq8i6ldl6 )
         	
         	The tibia equations have been gessed, but seem correct and working. A simulation of the physical 
         	tibia and the compensation for left and right leg has been made (link: https://www.desmos.com/geometry/2ujyudah5w)
         	
        */
        // 2024-04-03: messageCommand is not defined in hardware_interface.h!!
        
 // 2024-04-03: messageCommand is not defined in hardware_interface.h!!
        messageCommand.data[0]=(abs((-champ_cmd.points[0].positions[0]+OFFSET_03)*RAD2DEG))+5.12;//Shoulder
        messageCommand.data[1]=(0.3408*pow(champ_cmd.points[0].positions[1],2)+0.6434*(champ_cmd.points[0].positions[1])+0.0095)*RAD2DEG +10.0;//Femur -4deg
        messageCommand.data[2]=((champ_cmd.points[0].positions[2]-champ_cmd.points[0].positions[1]*ratio_pulleys_tibia+champ_cmd.points[0].positions[1]+1.658063)/ratio_pulleys_tibia)*RAD2DEG + 8;//Tibia

	//Front Right
        messageCommand.data[3]=(abs((-champ_cmd.points[0].positions[3]+OFFSET_03)*RAD2DEG))-2.0; //Shoulder
        messageCommand.data[4]=(-0.3593*pow(champ_cmd.points[0].positions[4],2)-0.6064*champ_cmd.points[0].positions[4]+2.375)*RAD2DEG +4.75;  //Femur
        messageCommand.data[5]=-(((champ_cmd.points[0].positions[5])-champ_cmd.points[0].positions[4]*ratio_pulleys_tibia+champ_cmd.points[0].positions[4])/ratio_pulleys_tibia*RAD2DEG)-5; //Tibia

	//Rear Left
        messageCommand.data[6]=(abs((champ_cmd.points[0].positions[6]+OFFSET_69)*RAD2DEG))-10.88;//Shoulder
        messageCommand.data[7]=(0.3408*pow(champ_cmd.points[0].positions[7],2)+0.6434*(champ_cmd.points[0].positions[7])+0.0095)*RAD2DEG + 5.3;//Femur
        messageCommand.data[8]=((champ_cmd.points[0].positions[8]-champ_cmd.points[0].positions[7]*ratio_pulleys_tibia+champ_cmd.points[0].positions[7]+1.658063)/ratio_pulleys_tibia)*RAD2DEG;//Tibia

	//Rear Right
        messageCommand.data[9]=(abs((champ_cmd.points[0].positions[9]+OFFSET_69)*RAD2DEG))+5.1;//Shoulder 1.1
        messageCommand.data[10]=(-0.3593*pow(champ_cmd.points[0].positions[10],2)-0.6064*champ_cmd.points[0].positions[10]+2.375)*RAD2DEG;//Femur
        messageCommand.data[11]=-(((champ_cmd.points[0].positions[11])-champ_cmd.points[0].positions[10]*ratio_pulleys_tibia+champ_cmd.points[0].positions[10])/ratio_pulleys_tibia*RAD2DEG);//-12.84;//Tibia
            }

        
            

    // Sending cmds with manual controller
    else if (ctrl_selector == true) {   // Unnecessary (should be replaced with else)
        messageCommand.data[leg_id] = leg_cmd;
    }
    
    JointState.header.stamp = ros::Time::now();
    JointState.name=champ_cmd.joint_names;
    JointState.position = champ_cmd.points[0].positions;
    /*
    for(int i = 0 ; i < 12 ; i++)
    {
		
		
    	
    }
	*/
    commandPublisher.publish(messageCommand);
    //ros::Duration(0.005).sleep();
    JointStatePublisher.publish(JointState);
}


int main(int argc, char** argv) {

    // Initialize the HWI node
    ros::init(argc, argv, "Bear_hardware_interface_node");
    ros::NodeHandle nh;
    
    // Separate Sinner thread for the Non Real-Time callbacks, such as service callbacks to load controllers
    ros::MultiThreadedSpinner spinner(2); 
    
    // Instanciate the robot's HWI and spin the thread 
    Bear Bear(nh);
    spinner.spin();
    
    return 0;
}

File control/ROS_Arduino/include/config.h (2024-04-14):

#ifndef CONFIG 
#define CONFIG 

#include <ros.h>

#include <std_msgs/UInt16.h>
#include <std_msgs/Float64.h>
#include <std_msgs/Float64MultiArray.h>
#include <std_msgs/Float32MultiArray.h>
#include <std_msgs/Int8MultiArray.h>
#include <std_msgs/String.h>
#include <controls/Servo_cmd.h>
//#include <controls/BNO.h>
//#include <Adafruit_Sensor.h>
//#include <Adafruit_BNO055.h>

#include <Servo.h> 
//#include "Wire.h"


// Potentiometers parameters
const long POT_MIN_VALUE = 0;
const long POT_MAX_VALUE = 1023;
const long POT_MIN_ANGLE = 0;
const long POT_MAX_ANGLE = 343;
const uint8_t NUMBER_OF_POTS = 12;

#define POT_PIN_ABD_AV_G A0
#define POT_PIN_FEM_AV_G A1
#define POT_PIN_TIB_AV_G A2
#define POT_PIN_ABD_AV_D A3
#define POT_PIN_FEM_AV_D A4
#define POT_PIN_TIB_AV_D A5
#define POT_PIN_ABD_AR_G A6
#define POT_PIN_FEM_AR_G A7
#define POT_PIN_TIB_AR_G A8
#define POT_PIN_ABD_AR_D A9
#define POT_PIN_FEM_AR_D A10
#define POT_PIN_TIB_AR_D A11
const int pot_id_array[NUMBER_OF_POTS] = {POT_PIN_ABD_AV_G, POT_PIN_FEM_AV_G, POT_PIN_TIB_AV_G,
                                          POT_PIN_ABD_AV_D, POT_PIN_FEM_AV_D, POT_PIN_TIB_AV_D,
                                          POT_PIN_ABD_AR_G, POT_PIN_FEM_AR_G, POT_PIN_TIB_AR_G,
                                          POT_PIN_ABD_AR_D, POT_PIN_FEM_AR_D, POT_PIN_TIB_AR_D};

// Servos parameters
#define NUMBER_OF_SERVOS 12

#define MOT_FEM_AV_D 2
#define MOT_TIB_AV_D 3
#define MOT_ABD_AV_D 4
#define MOT_FEM_AV_G 5
#define MOT_TIB_AV_G 6
#define MOT_ABD_AV_G 7
#define MOT_FEM_AR_D 8
#define MOT_TIB_AR_D 9
#define MOT_ABD_AR_D 10
#define MOT_FEM_AR_G 11
#define MOT_TIB_AR_G 12
#define MOT_ABD_AR_G 13

Servo ABD_AV_G, FEM_AV_G, TIB_AV_G, ABD_AV_D, FEM_AV_D, TIB_AV_D;
Servo ABD_AR_G, FEM_AR_G, TIB_AR_G, ABD_AR_D, FEM_AR_D, TIB_AR_D;

// BNO parameters
//uint16_t BNO055_SAMPLERATE_DELAY_MS = 100;
//Adafruit_BNO055 bno = Adafruit_BNO055(55, 0x28);

// ROS custom messages
std_msgs::String msg;
//controls::BNO bno_array;
//controls::Servo_cmd pot_value_array;

// Functions prototypes

// Servo
void servo_init();
void servo_cmd(const controls::Servo_cmd &cmd_msg);
// Potentiometers
//void pot_init(const int* pot_id_array);
controls::Servo_cmd pot_update(const int pot_id_array[NUMBER_OF_POTS]);
//void pot_feedback(const int pot_id_array[NUMBER_OF_POTS]);
//float long2float_map(long x, long IN_min, long IN_max, long OUT_min, long OUT_max);
// BNO
//void BNO_init();
//void bno_update();
//void bno_feedback(controls::BNO &feedback_array);

#endif

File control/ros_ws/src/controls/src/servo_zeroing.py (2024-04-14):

#! /usr/bin/env python3

from PyQt5 import QtCore as qtc
from PyQt5 import QtGui as qtgui
from PyQt5 import QtWidgets as qtw
# import qdarktheme
import rospy
from std_msgs.msg import Bool, Int8, Float32
import QFloatSliderEntryBox

show_GUI = rospy.get_param('/GUI/show_GUI') # Boolean parameter passed from CL

class Ui_MainWindow(object):
    def setupUi(self, MainWindow):
        MainWindow.setObjectName("MainWindow")
        MainWindow.setWindowTitle("servo-zeroing-GUI")
        MainWindow.resize(576, 720)
        MainWindow.setAutoFillBackground(False)

        # Create central widget
        self.central_widget = qtw.QWidget(MainWindow)
        self.central_widget.setObjectName("central_widget")
        self.boxLayout = qtw.QVBoxLayout(self.central_widget)
        
        # Set font
        qtgui.QFontDatabase.addApplicationFont("FiraCode-Regular.ttf")
        qtgui.QFontDatabase.addApplicationFont("FiraCode-Bold.ttf")
        font = qtgui.QFont()
        font.setFamily("Fira Code")
        font.setPointSize(14)

        # Create button that switches between controllers (i.e modes)
        self.control_switch_button = qtw.QPushButton(self.central_widget)
        self.control_switch_button.setGeometry(qtc.QRect(138, 500, 300, 40))
        self.control_switch_button.setFont(font)
        self.control_switch_button.setObjectName("control_switch_button")
        self.control_switch_button.setCheckable(True)
        self.control_switch_button.clicked.connect(self.switch_control_clicked)
        self.control_switch_button.clicked.connect(self.change_control_switch_color)
        self.change_control_switch_color()
        self.control_switch_button.setText("Controller: CHAMP")
        self.boxLayout.addWidget(self.control_switch_button)

        # Create a label showing which leg is currently being controlled
        self.leg_selection_label = qtw.QLabel(self.central_widget)
        self.leg_selection_label.setGeometry(qtc.QRect(88, 40, 400, 40))
        self.leg_selection_label.setFont(font)
        self.leg_selection_label.setObjectName("leg_selection_label")
        self.leg_selection_label.setText("Current leg: None")
        self.leg_selection_label.setAlignment(qtc.Qt.AlignHCenter)
        self.boxLayout.addWidget(self.leg_selection_label)

        # Create a warning label
        self.warning_label = qtw.QLabel(self.central_widget)
        self.warning_label.setGeometry(qtc.QRect(38, 480, 500, 40))
        self.warning_label.setFont(qtgui.QFont('Fira Code Bold', 14))
        self.warning_label.setAlignment(qtc.Qt.AlignCenter)
        self.warning_label.setObjectName("warning_label")
        self.boxLayout.addWidget(self.warning_label)
        
        # Create a grid layout for controls
        self.control_panel = qtw.QWidget(self.central_widget)
        self.control_panel.setDisabled(True)
        self.control_panel.setGeometry(qtc.QRect(38, 80, 500, 360))
        self.control_panel.setObjectName("control_panel")
        self.gridLayout = qtw.QGridLayout(self.control_panel)
        self.gridLayout.setContentsMargins(2, 2, 2, 2)
        self.gridLayout.setObjectName("gridLayout")

        # Create a combo box for selecting the leg controlled
        self.leg_selection_box = qtw.QComboBox(self.central_widget)
        self.leg_selection_box.setObjectName("leg_selection_box")
        self.leg_selection_box.addItems(["Avant Gauche", "Avant Droite", \
                                "Arrière Gauche", "Arrière Droite"])
        self.leg_selection_box.setFont(font)
        self.gridLayout.addWidget(self.leg_selection_box, 0, 0, 1, 2)
        
        # Create a float slider for the servo that controls the shoulder
        self.shoulder_slider_entry = QFloatSliderEntryBox.QFloatSliderEntryBox(
            qtc.Qt.Horizontal,
            invert_layout=False,
            id=0,
            decimals=2,
            regex="\-?\d{1,2}\.?\d{0,2}")
        self.shoulder_slider_entry._slider.setMinimum(-135.0)
        self.shoulder_slider_entry._slider.setMaximum(135.0)
        self.shoulder_slider_entry._slider.setSingleStep(0.05)
        self.shoulder_slider_entry._slider.setFont(font)
        self.shoulder_slider_entry._slider.valueChanged.connect(lambda: self.servo_update_cmd(self.shoulder_slider_entry._slider.getID(), self.shoulder_slider_entry._slider.getValue()))
        self.shoulder_slider_entry.setObjectName('shoulder_slider_entry')
        self.shoulder_slider_entry._entry.setFont(font)
        self.gridLayout.addWidget(self.shoulder_slider_entry, 1, 1, 1, 1)

        # Create a float slider for the servo that controls the femur
        self.femur_slider_entry = QFloatSliderEntryBox.QFloatSliderEntryBox(
            qtc.Qt.Horizontal,
            invert_layout=False,
            id=1,
            decimals=2,
            regex="\-?\d{1,2}\.?\d{0,2}")
        self.femur_slider_entry._slider.setMinimum(-135.0)
        self.femur_slider_entry._slider.setMaximum(135.0)
        self.femur_slider_entry._slider.setSingleStep(0.05)
        self.femur_slider_entry._slider.setFont(font)
        self.femur_slider_entry._slider.valueChanged.connect(lambda: self.servo_update_cmd(self.femur_slider_entry._slider.getID(), self.femur_slider_entry._slider.getValue()))
        self.femur_slider_entry.setObjectName('shoulder_slider_entry')
        self.femur_slider_entry._entry.setFont(font)
        self.gridLayout.addWidget(self.femur_slider_entry, 2, 1, 1, 1)

        # Create a float slider for the servo that controls the tibia
        self.tibia_slider_entry = QFloatSliderEntryBox.QFloatSliderEntryBox(
            qtc.Qt.Horizontal,
            invert_layout=False,
            id=2,
            decimals=2,
            regex="\-?\d{1,2}\.?\d{0,2}")
        self.tibia_slider_entry._slider.setMinimum(-135.0)
        self.tibia_slider_entry._slider.setMaximum(135.0)
        self.tibia_slider_entry._slider.setSingleStep(0.05)
        self.tibia_slider_entry._slider.setFont(font)
        self.tibia_slider_entry._slider.valueChanged.connect(lambda: self.servo_update_cmd(self.tibia_slider_entry._slider.getID(), self.tibia_slider_entry._slider.getValue()))
        self.tibia_slider_entry.setObjectName('shoulder_slider_entry')
        self.tibia_slider_entry._entry.setFont(font)
        self.gridLayout.addWidget(self.tibia_slider_entry, 3, 1, 1, 1)

        # Create labels for spin boxes
        self.shoulder_label = qtw.QLabel("Épaule: ")
        self.shoulder_label.setFont(font)
        self.gridLayout.addWidget(self.shoulder_label, 1, 0, 1, 1)

        self.femur_label = qtw.QLabel("Fémur: ")
        self.femur_label.setFont(font)
        self.gridLayout.addWidget(self.femur_label, 2, 0, 1, 1)

        self.tibia_label = qtw.QLabel("Tibia: ")
        self.tibia_label.setFont(font)
        self.gridLayout.addWidget(self.tibia_label, 3, 0, 1, 1)
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

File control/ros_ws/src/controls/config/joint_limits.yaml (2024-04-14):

joint_limits:

    FL_shoulder_servo:
      has_position_limits: true
      min_position: 0
      max_position: 15
      has_velocity_limits: false
      max_velocity: 0
      has_acceleration_limits: false
      max_acceleration: 0.0
      has_jerk_limits: false
      max_jerk: 0
      has_effort_limits: false
      max_effort: 0

    FL_femur_servo:
      has_position_limits: true
      min_position: 0
      max_position: 120
      has_velocity_limits: false
      max_velocity: 0
      has_acceleration_limits: false
      max_acceleration: 0.0
      has_jerk_limits: false
      max_jerk: 0
      has_effort_limits: false
      max_effort: 0
      
    FL_tibia_servo:
      has_position_limits: true
      min_position: 90
      max_position: 180
      has_velocity_limits: false
      max_velocity: 0
      has_acceleration_limits: false
      max_acceleration: 0.0
      has_jerk_limits: false
      max_jerk: 0
      has_effort_limits: false
      max_effort: 0

    FR_shoulder_servo:
      has_position_limits: true
      min_position: 0
      max_position: 15
      has_velocity_limits: false
      max_velocity: 0
      has_acceleration_limits: false
      max_acceleration: 0.0
      has_jerk_limits: false
      max_jerk: 0
      has_effort_limits: false
      max_effort: 0

    FR_femur_servo:
      has_position_limits: true
      min_position: 0
      max_position: 120
      has_velocity_limits: false
      max_velocity: 0
      has_acceleration_limits: false
      max_acceleration: 0.0
      has_jerk_limits: false
      max_jerk: 0
      has_effort_limits: false
      max_effort: 0
      
    FR_tibia_servo:
      has_position_limits: true
      min_position: 90
      max_position: 180
      has_velocity_limits: false
      max_velocity: 0
      has_acceleration_limits: false
      max_acceleration: 0.0
      has_jerk_limits: false
      max_jerk: 0
      has_effort_limits: false
      max_effort: 0

    RL_shoulder_servo:
      has_position_limits: true
      min_position: 0
      max_position: 15
      has_velocity_limits: false
      max_velocity: 0
      has_acceleration_limits: false
      max_acceleration: 0.0
      has_jerk_limits: false
      max_jerk: 0
      has_effort_limits: false
      max_effort: 0

    RL_femur_servo:
      has_position_limits: true
      min_position: 0
      max_position: 120
      has_velocity_limits: false
      max_velocity: 0
      has_acceleration_limits: false
      max_acceleration: 0.0
      has_jerk_limits: false
      max_jerk: 0
      has_effort_limits: false
      max_effort: 0
      
    RL_tibia_servo:
      has_position_limits: true
      min_position: 90
      max_position: 180
      has_velocity_limits: false
      max_velocity: 0
      has_acceleration_limits: false
      max_acceleration: 0.0
      has_jerk_limits: false
      max_jerk: 0
      has_effort_limits: false
      max_effort: 0

    RR_shoulder_servo:
      has_position_limits: true
      min_position: 0
      max_position: 15
      has_velocity_limits: false
      max_velocity: 0
      has_acceleration_limits: false
      max_acceleration: 0.0
      has_jerk_limits: false
      max_jerk: 0
      has_effort_limits: false
      max_effort: 0

    RR_femur_servo:
      has_position_limits: true
      min_position: 0
      max_position: 120
      has_velocity_limits: false
      max_velocity: 0
      has_acceleration_limits: false
      max_acceleration: 0.0
      has_jerk_limits: false
      max_jerk: 0
      has_effort_limits: false
      max_effort: 0
      
    RR_tibia_servo:
      has_position_limits: true
      min_position: 90
      max_position: 180
      has_velocity_limits: false
      max_velocity: 0
      has_acceleration_limits: false
      max_acceleration: 0.0
      has_jerk_limits: false
      max_jerk: 0
      has_effort_limits: false
      max_effort: 0

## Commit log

2024-01-19 GP-10 setup webots ros a continuer
    [my_robot.urdf]
2024-01-22 GP-10 webot ros2 first working setup
    [my_robot.urdf]
2024-01-29 GP-10 to test the leg trought arduino node
2024-01-30 GP-10 all legs setuped
2024-02-03 Controller initial setup.
    [controller.yaml, joint_limits.yaml]
2024-02-07 GP-37 cleansing
    [my_robot.urdf]
2024-02-08 installed champ ubuntu20.04 python3
    [Robot.urdf, ros_control.yaml]
2024-02-10 Le setup pour JointTrajectoryController est fait. Maintenant on doit faire les trajectoires.
    [controller.yaml, dawg_leg.urdf, trajectory_controller.yaml]
2024-02-11 Le dernier commit etait incomplet
    [trajectory_controller.yaml]
2024-02-11 J'ai renommer le trajectory_interface Le trajectory_interface fait maintenant l'envoie de goals via un action client Le hardware interface prend le goal pour faire des commande. Il manque seulement l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
2024-02-17 install script changes and robot cliping reduction
    [ros_control.yaml]
2024-02-21 champ arduino marche?
2024-02-21 Integration de Ros_control (Hardware interface+trajectory interface)
    L'etat actuel des choses:
    On envoie une commande par teleop
    La commande est traiter par CHAMP.
    Champ achemine une commande de type JointTrajectory
    Le Ros_control prend la commande, la convertie en
    float64multiarray, fait un goal et l'envoie avec via
    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
    [Robot.urdf, joint_limits.yaml, trajectory_controller.yaml]
2024-02-27 Add arduino
2024-02-27 push test
    [controller.yaml, trajectory_controller.yaml]
2024-03-04 Creation d'un launcher pour les trajectoire hardcoded. Le launcher initialise rosserial.
    roslaunch controls controls_TEST
2024-03-06 simul twin champ controller
    [Bear_twin.urdf]
2024-03-07 sim more sensors
    [ros_control.yaml]
2024-03-07 Les probleme de real-time sont resolu, avec un nouveau message leger pour les commandes. Beaucoup de chose sont commenter dans le code, afin de les garder en reference, ces commentaire seront enlever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
    [trajectory_controller.yaml]
2024-03-07 On calibre le mouvement de champ
2024-03-12 changes joints' type to revolute and adds limits to joints (to be modified later)
    [Robot.urdf]
2024-03-12 adds xacro files and modifies Robots.urdf to make it more compact by using macros
    [Robot.urdf, constant.xacro, include.xacro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]
2024-03-12 fixes syntax for button mapping lists
2024-03-12 Changement de parametre de frequence et de la boucle de controlle
    [ros_control.yaml]
2024-03-12 adds button mapping for PS3 controller
2024-03-13 updates 'tutorial' files and adds first draft of servo zeroing GUI
2024-03-20 fixes GUI launch problems
    [servo_zeroing.py]
2024-03-20 fixes control_switch_flag update problem
    [servo_zeroing.py]
2024-03-20 added calibration laucher
2024-03-22 Add lidar
2024-03-22 remove lidar
2024-03-22 fixes malloc problems with feedback_array; BNO should work properly
    [config.h]
2024-03-24 cleans up Arduino code
2024-03-28 Integration des potentiometre au hardware interface Debugging du publisher des potentiometre sur le arduino
2024-03-28 Integration du lidar
2024-03-28 La navigation par lidar semble fonctionner
2024-03-29 base angle traduction for legs realy done
2024-03-30 Changement de parametres pour la marche
    [Robot.urdf, ros_control.yaml]
2024-03-31 Arduino code for Calibration completted
2024-04-03 adds disabling functionnality to control_panel instead of showing error msg
    [servo_zeroing.py]
2024-04-03 cleans up a bit of code for Arduino
2024-04-03 updated urdf and robot description in the right axis (same as champ)
    [Robot_final.urdf, ros_control.yaml]
2024-04-03 Untested implementation of PCA driven servos
2024-04-03 fixes problem with servo related params and methods.
    [config.h, pub_sub.cpp]
2024-04-03 removes unnecessary params and methods for servos; essentially, it reverts the last commit.
    [config.h, pub_sub.cpp]
2024-04-03 On ramene le code arduino a sont etat initial
2024-04-03 arduino node makes a comeback
2024-04-07 changed champ url for install script. calibration is complette
2024-04-07 Ajustement zero software des femurs dans le HWI
2024-04-10 removes BNO code from Arduino Mega project; adds new Arduino Nano project for BNO.
2024-04-10 La marche est bonne. Ajout d'un launch pour le pi (controls_pi.launch) On essai de faire runner avec le Pi
2024-04-10 L'odometrie fonctionne!!! Mais c'est pas parfait.
2024-04-14 'Merged' CAD files from branch 'GP-6-Tibia'
    [0_0_1_belt_6mmShaft_1.SLDPRT, 0_0_1_belt_6mmX15mmShaft_1.SLDPRT, 0_0_1_belt_6mm_manivelle_1.SLDPRT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]
2024-04-14 The last commit on earth
    [Bear_twin.urdf, Robot.urdf, Robot_final.urdf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]
2024-04-14 Les conflict sont resolu. C'etait pas trop pire actually. Bonne chance a la prochaine cohorte de GRO qui vont vouloir nous "one-up"

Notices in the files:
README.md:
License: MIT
